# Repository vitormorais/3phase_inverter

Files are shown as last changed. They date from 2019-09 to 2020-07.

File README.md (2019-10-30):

# 3-phase Power Inverter Development Repository

### Important Information for SELE

- The guide to use the setup is presented in [Guide](https://github.com/vitormorais/3phase_inverter/raw/master/1.%20Functional/guide.docx)
- The repository to import with DAVE is present in [DAVE Project](https://github.com/vitormorais/3phase_inverter/raw/master/4.%20Software_WS/SELE_initialProject.zip)

### Features

- The 3-phase 30A@450V power inverter for academic/research purposes;
- This inverter has built-in measurements of AC currents, AC voltages and DC bus voltage;
- The inverter is based on infineon IPM IKCM30F60GA module (a low-cost module, with integrated drivers);
- The control board is based on XMC4500 Relax (lite) kit, a well known board in UP Laboratory of Power Electronics;
- Reduced cost of hardware (around 100€);

### Motivation

- Decrease the Hardware design, by using a generic multi-purpose power inverter;
- Decrease the Testing time and increase the Validation outcomes;
- Increase in Implementation and Control capabilities, without spending too much time in this step;
- Increase in new contributions to the Scientific Comunity, with more papers.

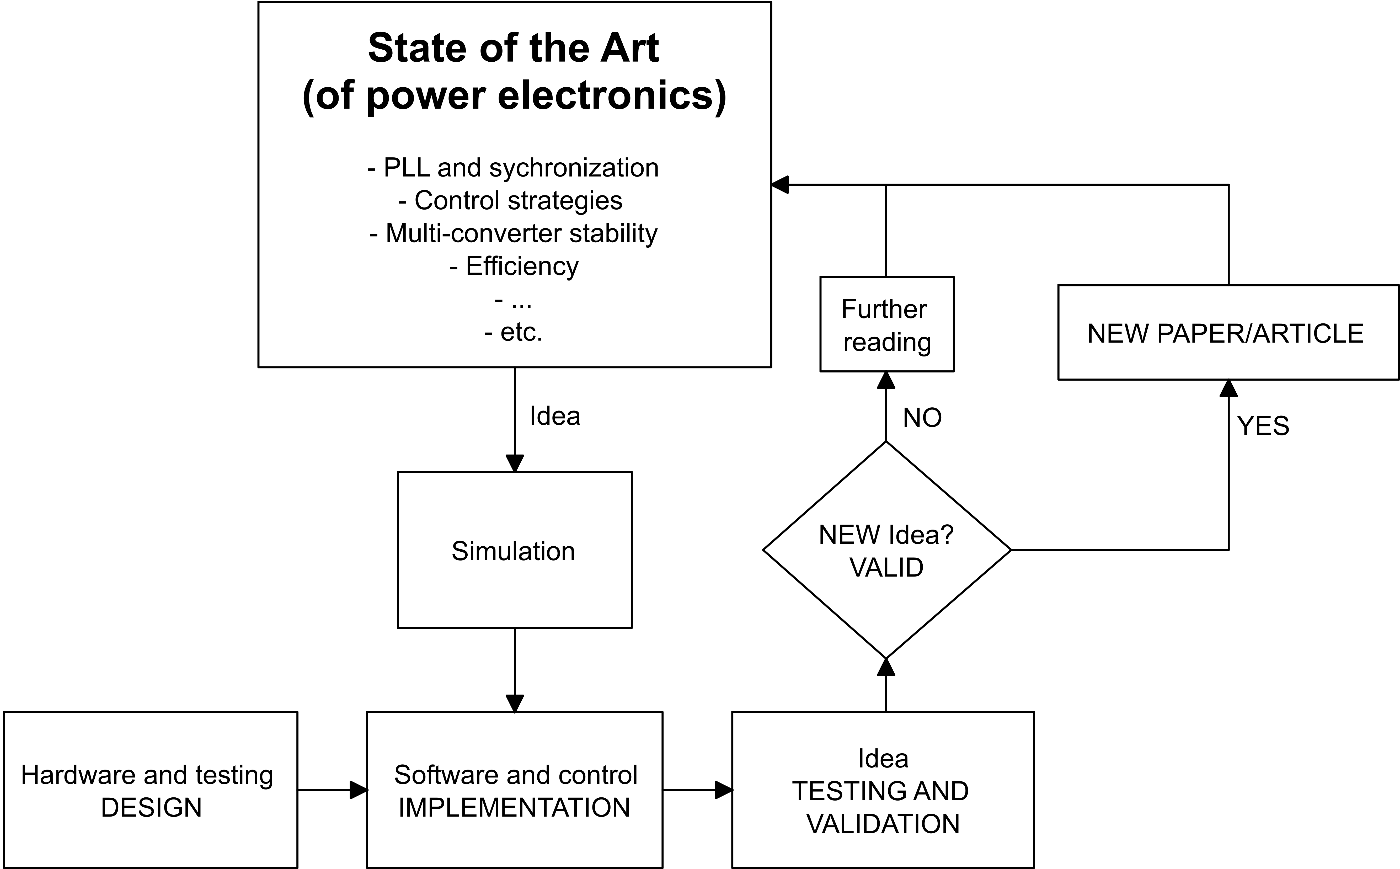
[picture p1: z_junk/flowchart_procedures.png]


------------

### How to use

- TODO

### TODO

- Define functional requirements of this project
- Create BOM for 10 boards (expecting 1000€)
-
- Create "how to use" manual 

------------

### DEMO

#### V2
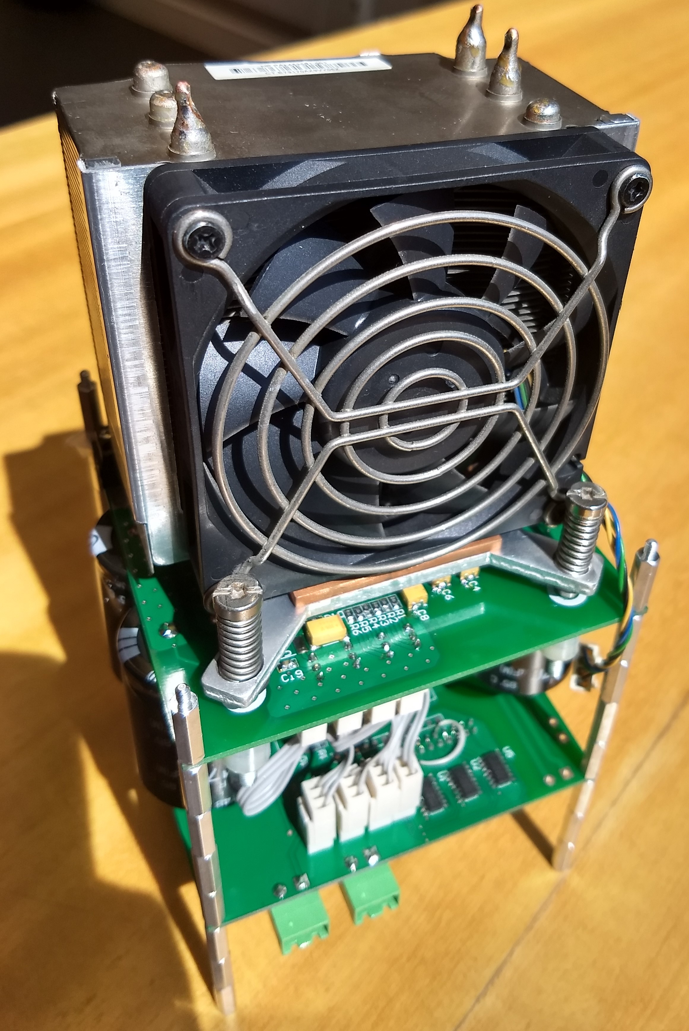
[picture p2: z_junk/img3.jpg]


#### V1
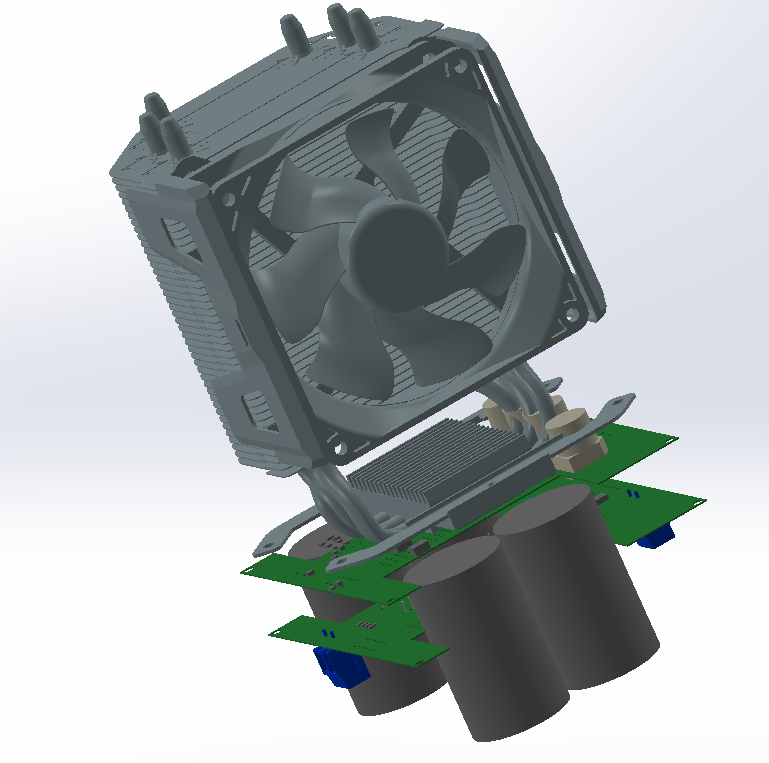
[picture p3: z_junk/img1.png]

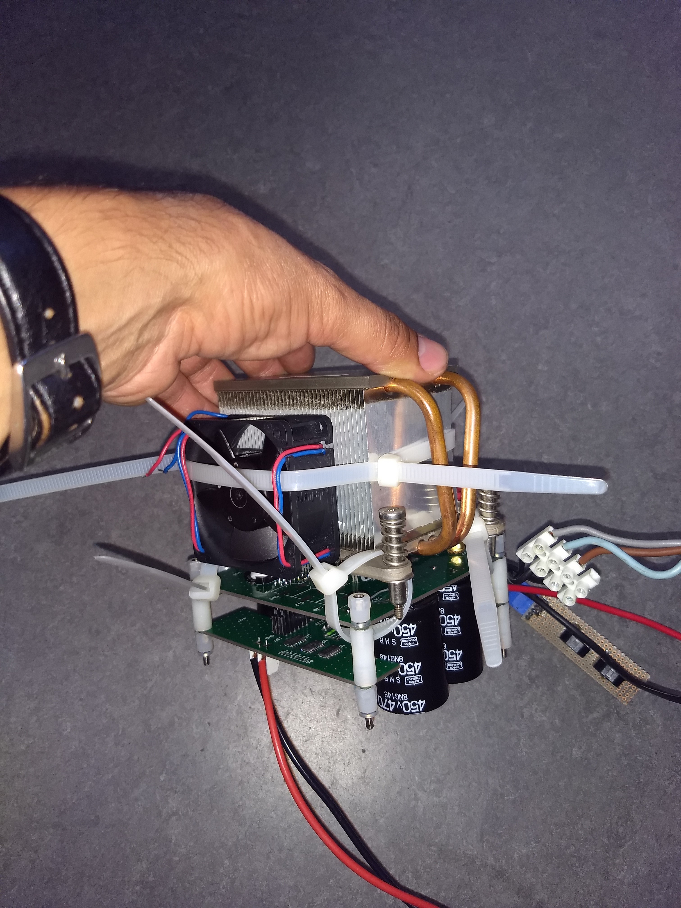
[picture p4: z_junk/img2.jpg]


------------

### Folder structure

| FOLDER | DESCRIPTION  | comments  |
| :--- | :--- | :--- |
|  1. Functional  |  Documentation folder for functional requirements of this project | |
|  2. Hardware PCB  |  Development folder for the PCB hardware  | |
|  3. Design  |  Documentation for the hardware design requirements and BOM | |
|  4. Software_WS  |  Development folder having the DAVE workspace for XMC4500 programming  | |
|  5. Implementation | Documentation and simulation of the simulated models/algorithms |  |
|  6. Testing&Validation | Documentation of the product testing | |
|  z_junk |  folder for not-structured content | | 

### Folder structure (tree)

```bash
├── 1. Functional
│   └── draft.docx
├── 2. Hardware PCB
│   ├── CAMtastic_controlo_rev21.Cam
│   ├── CAMtastic_controlo_rev22.Cam
│   ├── CAMtastic_inversor_rev21.Cam
│   ├── CAMtastic_inversor_rev22.Cam
│   ├── History
│   ├── PCB_controlo_rev2.zip
│   ├── PCB_inversor_rev2.zip
│   ├── __Previews
│   ├── accets
│   ├── controlo_rev2.PcbDoc
│   ├── controlo_rev2.PrjPcb
│   ├── controlo_rev2.PrjPcbStructure
│   ├── controlo_rev2.SchDoc
│   ├── debug.log
│   ├── inversor_rev2.PcbDoc
│   ├── inversor_rev2.PrjPcb
│   ├── inversor_rev2.PrjPcbStructure
│   ├── inversor_rev2.SchDoc
│   ├── vmorais_libraries.PcbLib
│   └── vmorais_libraries.SchLib
├── 3. Design
│   └── BOM.xlsx
├── 4. Software_WS
│   └── OL_VSC_vitor
├── 5. Implementation
│   └── hardware.psimsch
├── 6. Testing&Validation
│   └── testing.docx
├── README.md
├── folder_structure_binary.txt
└── z_junk
    ├── flowchart_procedures.png
    ├── flowchart_procedures.svg
    ├── img1.png
    ├── img2.jpg
    └── img3.jpg
```

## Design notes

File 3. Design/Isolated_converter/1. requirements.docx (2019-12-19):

List of requirements

1. All measurments should be isolated
  a. Current measurement isolation: achieved;
  b. Voltage measurement isolation: achieved;
  c. DC bus voltage measurement: achieved;
  d. Termistor temperature measurement: not achieved
    i. An isolation amplifier should be considered
  e. Fault: to be considered
2. All of the driving signals/pwm should be isolated
  a. Include an isolation DC/DC converter
3. The IPM module must be supplied by an isolation DC/DC converter
  a. Include an isolation DC/DC converter (15.5V)
4. Avoid/reduce the amount of cables
  a. Promote the usage of jumpers

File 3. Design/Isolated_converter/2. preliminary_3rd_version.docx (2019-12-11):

This document presents the possible solution for the final prototype of the converter.

A possible solution will be a middle board between the already developed board and the new board:

1. Consider there the isolation part
2. DC/DC 6W 5V (in: 18 V to 36 V): https://pt.mouser.com/ProductDetail/MEAN-WELL/SCWN06B-05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
3. DC/DC 6W 15V (in: 18 V to 36 V): https://pt.mouser.com/ProductDetail/MEAN-WELL/SCWN06B-15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
4. Considerar o seguinte amplificador de isolamento para medir a temperatura do termistor e a tensão do barramento DC:
  a. http://www.ti.com/product/AMC1211-Q1
5. Atuar relés com dual gate drivers (0,76€):
  a. Relés: Mouser No:653-G6DN-1A-SL-DC5
  b. https://eu.mouser.com/ProductDetail/Microchip-Technology-Micrel/MIC4126YME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
6. Usar isolador digital
7. Usar individual gate drivers (0,864€):
  a. https://eu.mouser.com/ProductDetail/Microchip-Technology-Micrel/MIC44F18YMME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
  b. A tensão de alimentação tem de ser, no máximo, 10V
  c. Corrigido para o seguinte integrado:
  d. https://eu.mouser.com/ProductDetail/IXYS/IX4340NETR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
  e. Circuito lógico para um dos braços: https://circuitverse.org/users/14109/projects/41676
  f. Necessárias 15 nand gates
8. Necessário uma fonte de 5V para o XMC4500 (24->5V não isolada)
9. Necessária uma fonte não isolada 15v-5v para alimentar o circuito de 5V do IPM
10. Necessário manter o circuito de drive, sem enables, com uma resistência no braço superior de 0ohm que permita ligar o sinal de gate do transistor de cima à massa

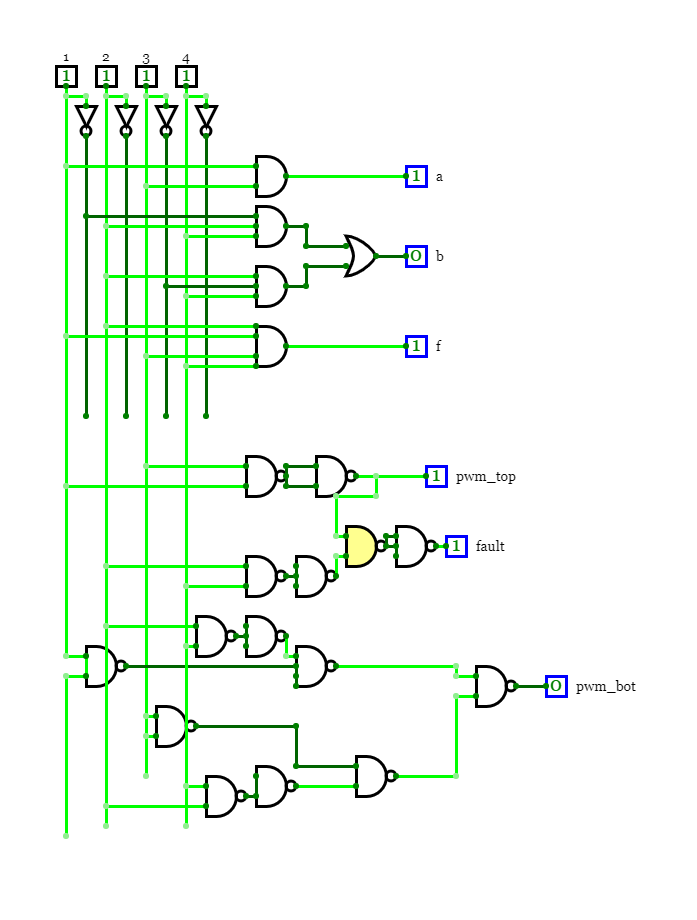
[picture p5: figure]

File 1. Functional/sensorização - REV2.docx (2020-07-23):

# Sensorização - REV2.0

Este documento identifica as lições aprendidas com os sensores empregados no conversor trifásico.

## Sensores de corrente

Foram utilizados sensores directamente ligados aos ADCs. Relativamente aos sensores internos de corrente, foi usado um divisor resistivo para atenuação

Esta estratégia funciona, mas pode facilmente ser melhorada. Por exemplo, a escolha de uma tensão de 3.3V não foi a melhor já que os sensores não estão a funcionar dentro das gamas recomendadas.

1. A escolha do sensor tipo SOIC8 é interessante e poderá ser mantida para correntes até +/- 30A.
2. Poderá ser equacionado ter uma PCB com duas footprints: uma para os sensores SOIC8 e outra para os sensores tipo Alegro 200A. Para correntes superiores, dessolda-se o SOIC8 e solda-se o outro. Do ponto de vista de sensorização, em tese, ambos têm a mesma saída.
3. Layers de electrónica:
  a. A primeira layer após o sensor deverá ser um buffer;
  b. De seguida deverá existir um RC com frequência de corte na ordem de 100kHz;
  c. Then, um circuito amplificador com ganho controlado digitalmente, a ser estudado
  d. Finalmente, toda a electrónica precisa de uma alimentação fixa. Provavelmente a mais indicada deverá ser 5V. Se os sensores precisarem de 3.3V, então, deverão existir reguladores.
4. Para cabo, pode ser equacionada a opção RJ45 blindado CAT7
  a. 1.48€: 1M https://www.castroelectronica.pt/product/cabo-de-rede-rj45-cat7-sftp-1m-cinzento--aisens
  b. Cada conector: 0,66€; do lado do controlo podem ser usados conectores múltiplos

## LOGBOOK sensores de corrente

V0.2 revisão do circuito analógico

Deverá ser alterado o circuito para um amplificador não inversor (senão não funciona)

V0.1

Fig1: esquemático raw, todas as ideias em cima da mesa

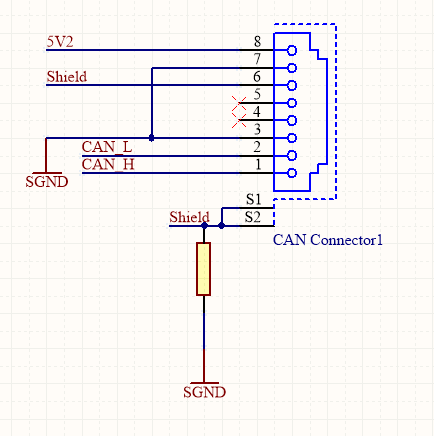
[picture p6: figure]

Fig2: detalhe da implementação atual do CAN

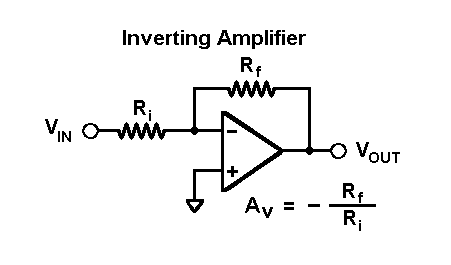
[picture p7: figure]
What is inverting amplifier? - Quora
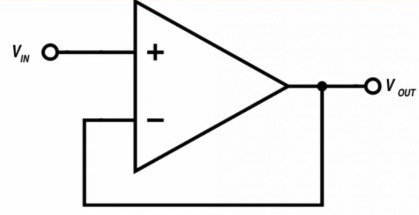
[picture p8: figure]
Applications of the Op-Amp Voltage Follower Circuit - Video Tutorial
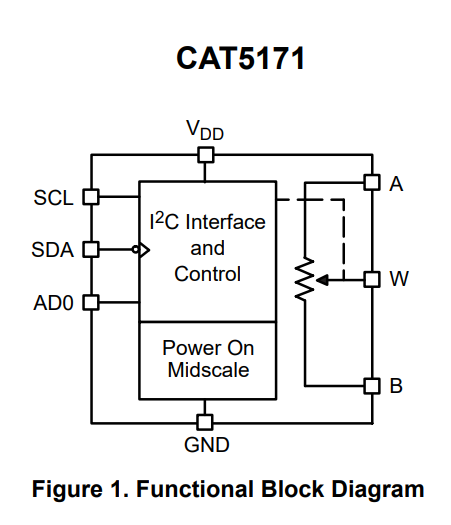
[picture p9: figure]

Fig3: esquemas importantes p/ electrónicas

Tabela 1: Estudo dos custos

funcionalidade | IC | link | custo
Sensor 1 | ACS712ELCTR-20A-T | C10681 (https://lcsc.com/product-detail/Sensors_Allegro-MicroSystems-LLC_ACS712ELCTR-20A-T_Allegro-MicroSystems-LLC-ACS712ELCTR-20A-T_C10681.html/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) | 1,22€ x3
Sensor 1 | ACS770ECB-200B-PFF-T | | 7€ x3
3x buffer + | OPA2350 | C55904 (https://lcsc.com/product-detail/Precision-OpAmps_TI_OPA2350UA-2K5_OPA2350UA-2K5_C55904.html/?href=jlc-SMT) | 3x 1.27€
3x amplifier | OPA2350 | C55904 (https://lcsc.com/product-detail/Precision-OpAmps_TI_OPA2350UA-2K5_OPA2350UA-2K5_C55904.html/?href=jlc-SMT) | 3x 1.27€
3x variable gain | 50 kohm i2c DIGITAL POTENTIOMETER | C154777 (https://lcsc.com/product-detail/Digital-Potentiometer-ICs_ON-Semicon_CAT5171TBI-50GT3_ON-Semicon-ON-CAT5171TBI-50GT3_C154777.html/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) | 3x 0.3679€
5V LDO (?)
3.3V LDO (?)
Microcontroller | STM32F103C8T6 | C8734 (https://lcsc.com/product-detail/ST-Microelectronics_STMicroelectronics_STM32F103C8T6_STM32F103C8T6_C8734.html/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) | 1.3€
OSC uC 16 MHz | X322516MLB4SI | C13738 (https://lcsc.com/product-detail/SMD-Crystal-Resonators_Yangxing-Tech-X322516MLB4SI_C13738.html/?href=jlc-SMT) | 0.08€
CAN (provavelmente n/ isolado) | TJA1050T/CM,118 | C6952 (https://lcsc.com/product-detail/CAN_NXP_TJA1050T-CM-118_TJA1050T-CM-118_C6952.html/?href=jlc-SMT) | 0,396€
Conector RJ45 c/ leds | RJE49-188-1411 | mouser | 4,18€
RC: 100ohm 100pF | Dá 150kHz

Total PCB + ASM aprox 12€

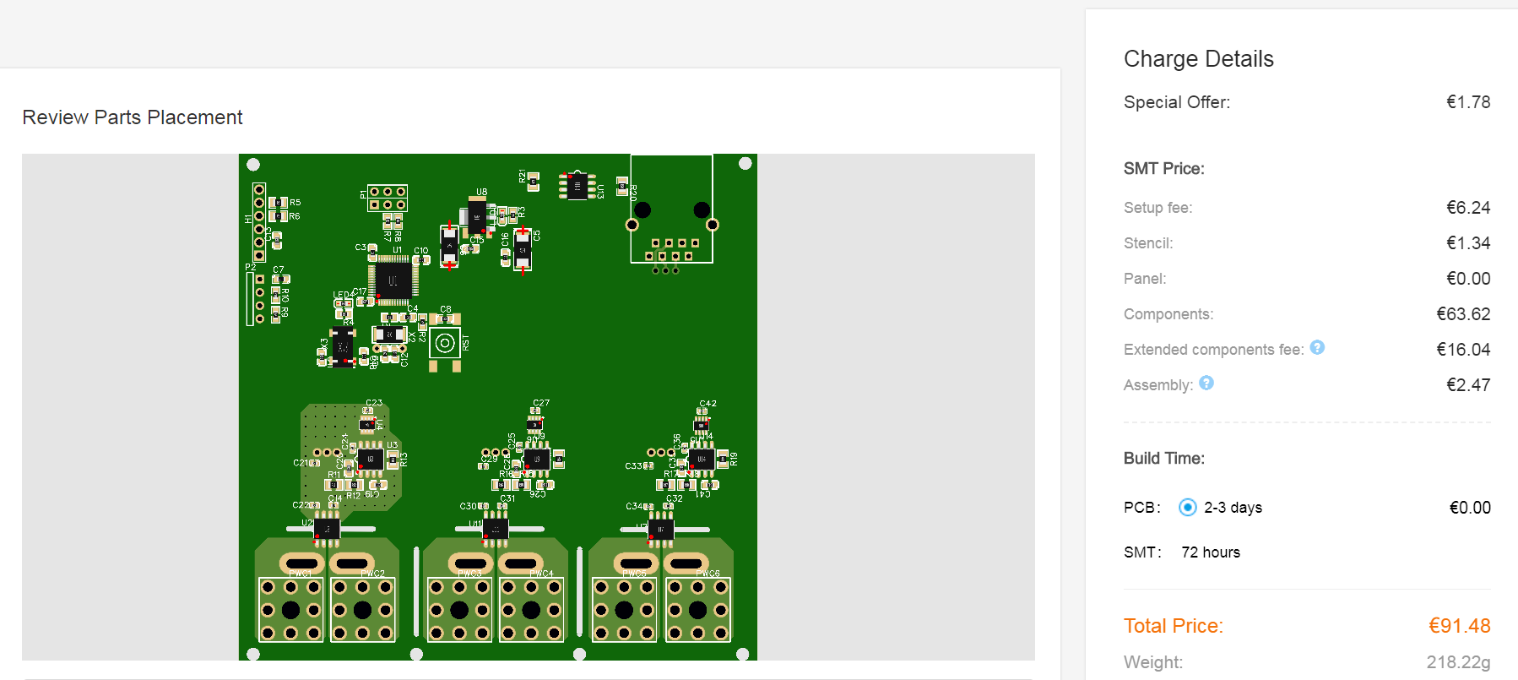
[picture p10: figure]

Preço p/ 10 placas= 160€ aprox (inc. shipping + alfandega)

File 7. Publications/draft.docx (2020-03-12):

# Title

Three-phase Power Inverter for academic purposes: lessons learned from teaching electronics.

# Abstract

Teaching power electronics adequately is a complex task.

Within the strategies found in the literature, the one used in this work includes the use of a simulator. (ver possível plágio do paper do Valter)

This simulator represents the hardware platform for a three-legs inverter, with integrated current and voltage measurements.

Currently, the simulator supports an infineon XMC4500 control board, where the same .c code is used either in the simulator and in the control board.

The hardware setup was first used at a Power Electronics course of the Integrated Master Degree in Electrical and Computing Engineering at the Faculty of Engineering of the University of Porto.

The results of this hardware setup usage in this course shows the students learning process, where several fields of power electronics were acquired, such as control loops, input measurements processing, etc.

In this work, the materials and methods to adequately teach either the simulator and the hardware setup will be presented and discussed.

# Introduction

# Literature review

# Materials

Hardware:

- The 3-phase 30A@450V power inverter for academic/research purposes;
- This inverter has built-in measurements of AC currents, AC voltages and DC bus voltage;
- The inverter is based on infineon IPM IKCM30F60GA module (a low-cost module, with integrated drivers);
- The control board is based on XMC4500 Relax (lite) kit, a well known board in UP Laboratory of Power Electronics;

Software:

- PSIM
- .c block
- Libraries

# Methods

## Step 1: practical demonstration of an example implementation

In this step, an example application of one simple capability is presented and is supported with a guide. It is expected that this step will take 2x 2h

This example considers the hardware setup connected to a 30V DC bus, and the three-phase outputs connected to a RL load. The objective of this demonstration example is to generate an AC output voltage in the inverter, that will be seen as an AC current in the RL load.

The simulation example will have all hardware modelling and a .c block with the code ready to generate the output desired waveforms.

## Step 2: theorical presentation of the libraries

In this step, a few libraries will be presented for general purpose implementations. In this set of libraries, PI controllers, first order low pass filters, Park/Clark transformations, delays, etc are presented.

## Step 3: presentation of the possible applications

In this step, each of the possible applications of power electronics converters that can be implemented with this three-leg converter are presented.

Examples:

- three phase induction motor control;
- three phase inverter
- single phase motor control
- single phase inverter
- DC motor control
- 3x regulated step-down voltage sources
- Interleaved DC/DC step down converter
- Step-up converter for PV applications
- Bi-directional battery charger

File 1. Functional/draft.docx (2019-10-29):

# Sumário

Este documento apresenta as linhas gerais de um projeto focado no desenvolvimento de uma plataforma de desenvolvimento destinada à investigação e/ou ensino de métodos de controlo para conversores eletrónicos de potência, especificamente, inversores.

# Objetivo

Este inversor deverá ser capaz de:

1. Funcionar como amplificador de potência programável com três saídas de sinal (inversor trifásico) e uma entrada de um barramento DC
  a. Deverá proporcionar ensaios sobre cargas trifásicas
2. Funcionar como fonte de corrente controlada
  a. Deverá ser capaz de controlar a corrente de uma carga, independentemente da tensão de alimentação
3. Ter flexibilidade para ligação à rede trifásica
  a. deverá ter contactores ()
  b. deverá ter medida de tensão

Este inversor deverá ser

1. Modular, com drives e comando integrados (tecnologia IPM)
2. Sensorização integrada:
  a. de 3 correntes AC, da tensão DC (obrigatório)
  b. de 3 tensões AC (apenas nos módulos de ligação trifásica)
3. Dotado de algumas protecções
  a. Contactores/relés, apenas se houver necessidade funcional
  b. Desde que não encareça o custo da solução
4. Microcontrolador integrado na solução

Com este inversor, deverá ser submetido um paper para uma conferência na área de PE, possivelmente focado na componente de educação

# Tarefas

1. Desenvolvimento de uma lista de requisitos da solução final
2. Desenvolvimento de esquemas

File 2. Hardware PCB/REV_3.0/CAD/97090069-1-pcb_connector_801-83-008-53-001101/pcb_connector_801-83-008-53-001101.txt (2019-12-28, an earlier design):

"Symbol";"Value";"Unit";
"TraceParts.PartNumber";"10-20122013-099820";"";
"REFERENCE";"801-83-008-53-001101";"";
"TraceParts.PartTitle";"Wire-wrap socket connector 2.54 mm, height 7 mm, 3-level, single row";"";
"TraceParts.InstanceId";"10-20122013-0998203EZ7EX63LKH9MCDKNJ7ZAHDI6";"";
"DESIGN";"Wire-wrap socket connector 2.54 mm, height 7 mm, 3-level, single row, 8 contacts, Tin / 0,75 µm Gold";"";
"TraceParts.PartStatus";"Published";"";
"TraceParts.PartStatusId";"";"";
"SUPPLIER";"preci-dip";"";
"TraceParts.PartVersion";"1.0.6";"";
"TRACEPARTS";"TRACEPARTS";"";
"TraceParts.PartLanguage";"en";"";
"TraceParts.ClassPath";"PRECIDIP:/F_PRECIDIP/PRECIDIP.020/PRECIDIP.020.060/10-20122013-099820";"";

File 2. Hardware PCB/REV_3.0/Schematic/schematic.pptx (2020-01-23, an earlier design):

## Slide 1

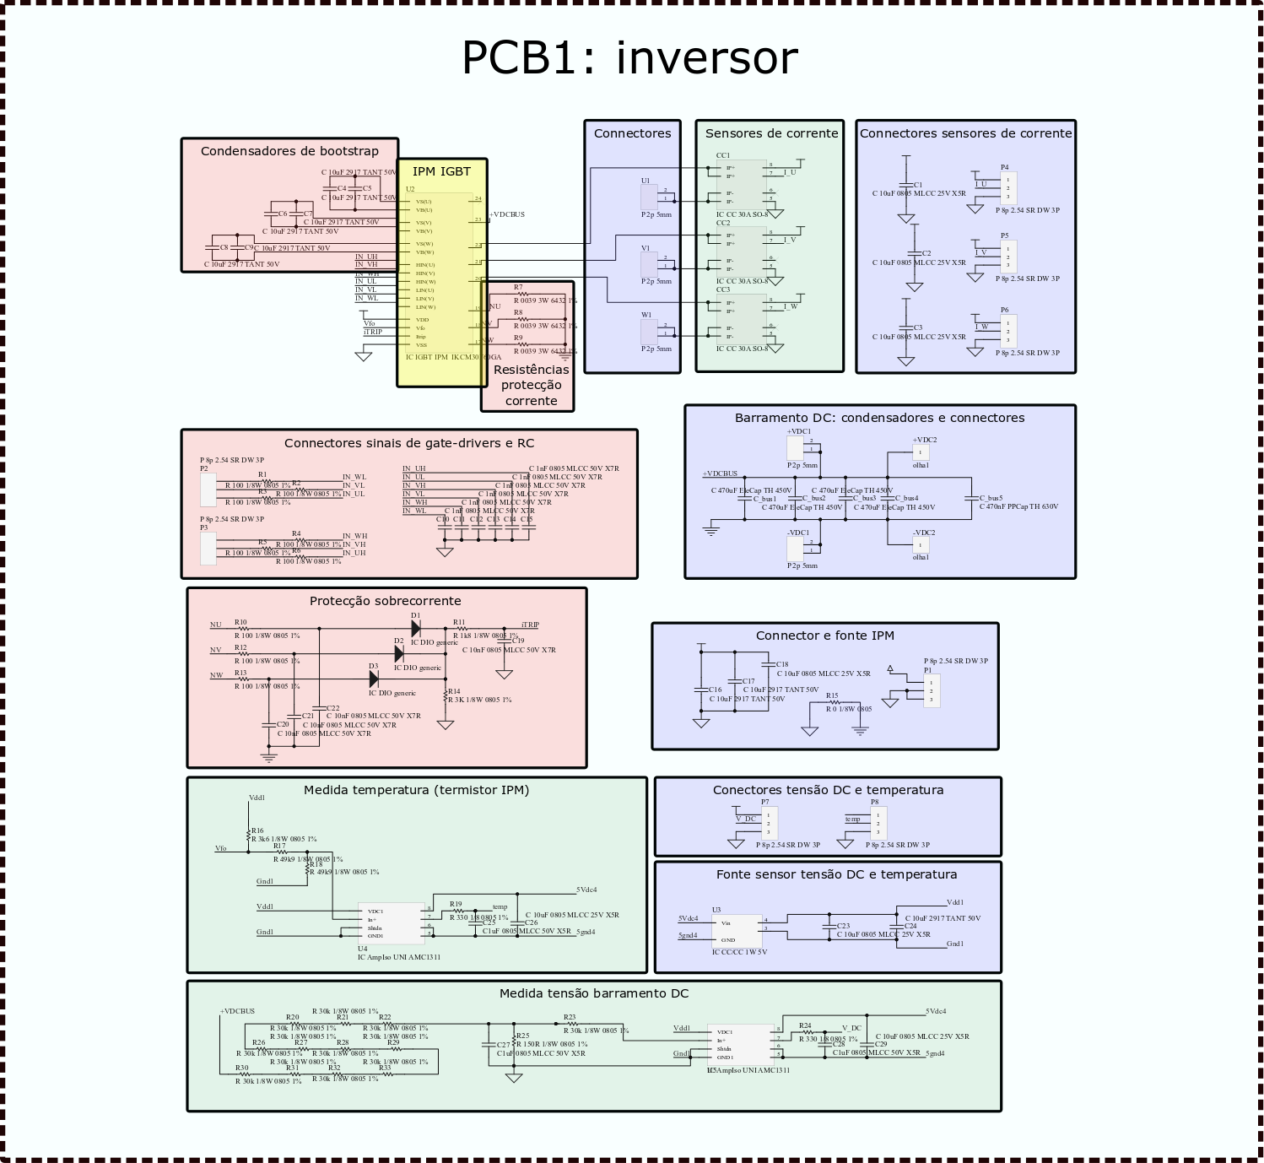
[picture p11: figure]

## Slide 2

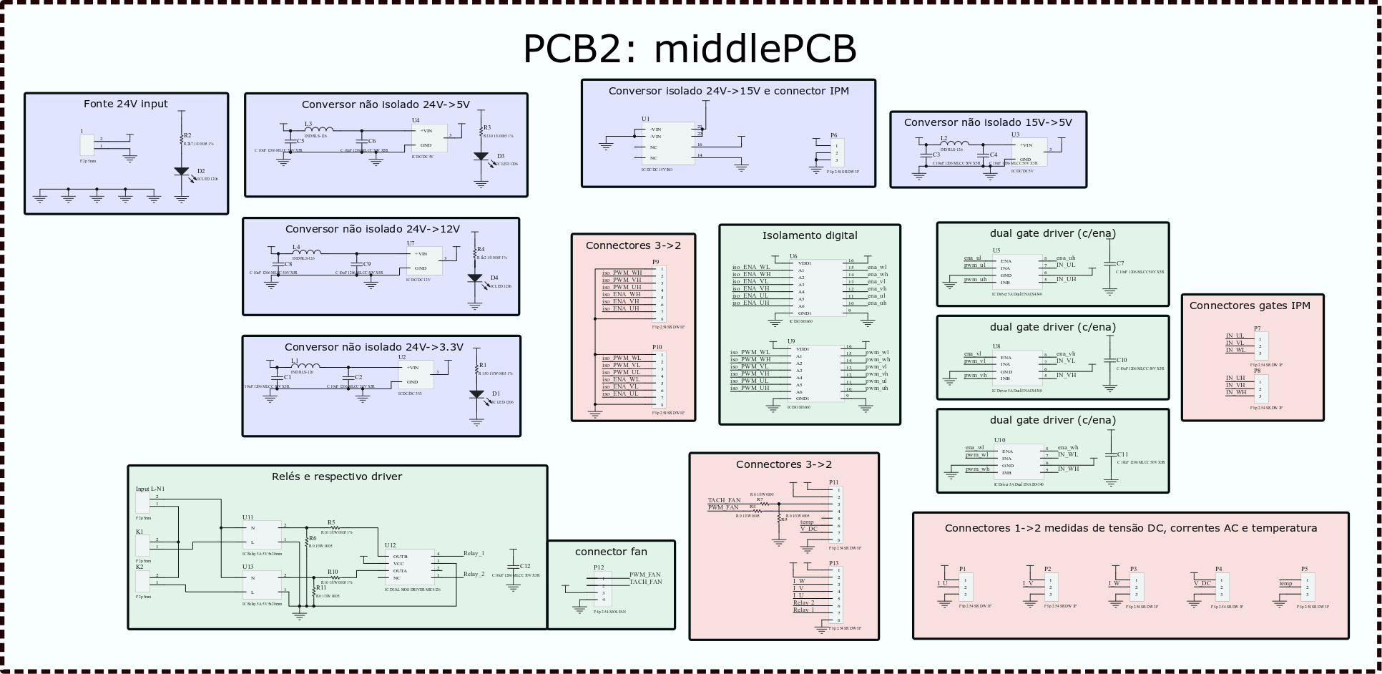
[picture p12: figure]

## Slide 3

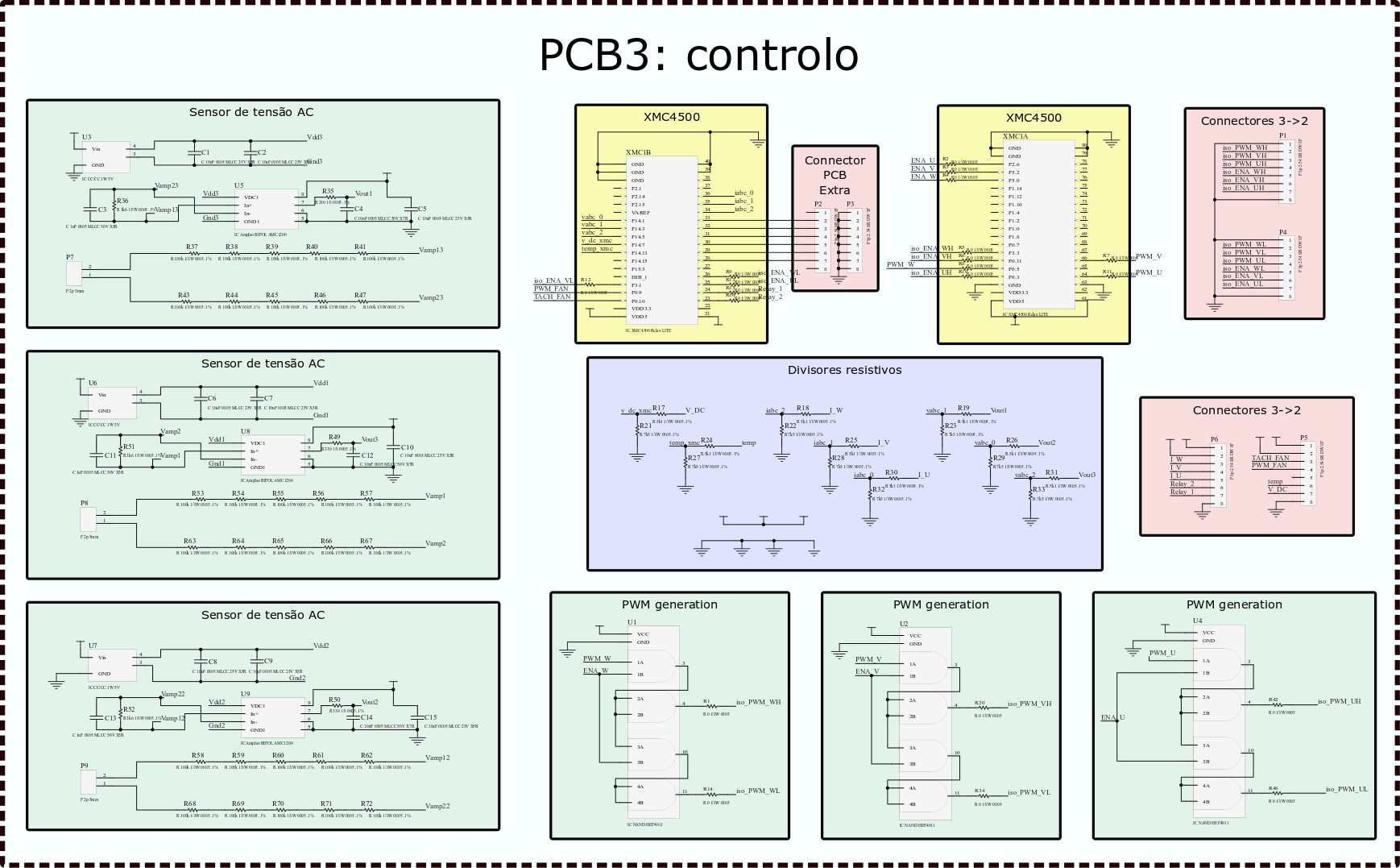
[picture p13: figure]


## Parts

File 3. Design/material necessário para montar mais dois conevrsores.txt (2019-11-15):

temos capacidade de montar mais dois conversores:
---  1 sem medida de tensões AC
---  1 com medida de tensões AC (igual aos demais)

faltam os seguintes componentes:
-- crimps (só dá para fazer 1 conversor)
-- alojamento para crimps (não chega a 1)
-- header para crimps (dá para 1)
-- conector pcb parafuso (pode ser utilizado phoenix)
-- xmc4500 (a pedir na i103)
-- barra de pinos fêmea pcb (a pedir no RC)
-- espaçadores de plástico: a pensar numa estrutura em 3D

resumindo, há capacidade de construção de dois conversores, mas são preciso alguns truques

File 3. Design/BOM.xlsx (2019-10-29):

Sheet: Sheet4
fornecedor | VPN | Description | Quantity | price | price total
RS | 896-6696 | Bloque de terminal PCB, paso5mm 2 Contacto Macho Recta Bloque de terminales PCB, montaje: Montaje en PCB | 20 | 0.240 € | 4.80 €
MOUSER | 963-UMK316BBJ106ML-T | Capacitores de cerâmica multicamada MLCC - SMD/SMT 1206 50V 10uF 20% X5R | 20 | 0.310 € | 6.20 €
MOUSER | 80-T491D106K050AT | Condensadores de tântalo - revestimento sólido de SMD 50V 10uF 10% ESR=0.8Ohms | 20 | 1.580 € | 31.60 €
MOUSER | 603-CC805KRX7R9BB103 | Capacitores de cerâmica multicamada MLCC - SMD/SMT 10nF 50V X7R 10% | 50 | 0.051 € | 2.55 €
MOUSER | 963-TMK212BBJ106KG-T | Capacitores de cerâmica multicamada MLCC - SMD/SMT 10uF 25V X5R +/-10% 0805 Gen Purp | 60 | 0.108 € | 6.48 €
MOUSER | 963-UMK212BJ105MG-T | Capacitores de cerâmica multicamada MLCC - SMD/SMT 0805 50V 1uF 20% X5R | 50 | 0.061 € | 3.05 €
MOUSER | 630-ACHS-7123-000E | Sensores de Corrente de Montagem de Painel Hall Effect IC LF 30A 66 mV/A | 10 | 2.770 € | 27.70 €
MOUSER | 661-ESMR451N471MR40S | Capacitores eletrolíticos de alumínio - terminal de pressão 450V 470uF 20% Tol. | 20 | 5.580 € | 111.60 €
FARNELL | 9751343 | B32653A6474K000 - DC Film Capacitor, 0.47 µF, 630 V, Metallized PP, ± 10%, B32653 Series | 2 | 2.180 € | 4.36 €
MOUSER | 512-1N4148TR | Diodos - Fins gerais, energia, comutação Hi Conductance Fast | 20 | 0.050 € | 1.00 €
MOUSER | 538-105431-1103 | Distribuidores e Alojamento de Fios NANO-FIT HDR SMT VT SGL 3CKT TIN BLK | 20 | 1.490 € | 29.80 €
MOUSER | 538-145130-0300 | Cabos de força DC Nano-Fit 75mm Cbl SR 3Ckt Blk | 10 | 2.920 € | 29.20 €
FARNELL | 1675765 | MC34631 - Wire-To-Board Connector, Vertical, 2.54 mm, 3 Contacts, Header, MC34 Series, Through Hole, 1 Rows | 50 | 0.029 € | 1.46 €
FARNELL | 1675755 | MC34483 - Connector Housing, MC34 Series, Receptacle, 3 Ways, 2.54 mm, 2218T Crimp Contacts | 50 | 0.028 € | 1.38 €
RS | 467-598 | Contacto de terminal de crimpado Molex 08-50-0032, KK, 4809, Hembra, Crimpado, Revestimiento de Estaño | 200 | 0.078 € | 15.60 €
MOUSER | 71-CRCW0805100RFKEAC | Resistores de Filme Espesso - SMD 1/8Watt 100ohms 1% Commercial Use | 50 | 0.047 € | 2.35 €
FARNELL | 2828259 | MCLRP12FTWRR039 - SMD Current Sense Resistor, 0.039 ohm, LRP Series, 2512 [6432 Metric], 3 W, ± 1%, Metal Strip | 20 | 0.257 € | 5.14 €
MOUSER | 652-CR0805JW-362ELF | Resistores de Filme Espesso - SMD 3.6K 5% | 10 | 0.034 € | 0.34 €
MOUSER | 71-CRCW08051K00FKEAC | Resistores de Filme Espesso - SMD 1/8Watt 1Kohms 1% Commercial Use | 10 | 0.055 € | 0.55 €
MOUSER | 755-ESR10EZPJ182 | Resistores de Filme Espesso - SMD 0805 1K8ohm 5% Anti Surge AEC-Q200 | 10 | 0.064 € | 0.64 €
MOUSER | 667-ERJ-6GEYJ302V | Resistores de Filme Espesso - SMD 0805 3Kohms 5% Tol AEC-Q200 | 10 | 0.055 € | 0.55 €
MOUSER | 71-CRCW08050000Z0EAC | Resistores de Filme Espesso - SMD 1/8Watt 0ohms Commercial Use | 10 | 0.026 € | 0.26 €
MOUSER | 667-ERJ-6ENF3002V | Resistores de Filme Espesso - SMD 0805 30Kohms 1% AEC-Q200 | 200 | 0.020 € | 4.00 €
MOUSER | 71-CRCW0805330RFKEAC | Resistores de Filme Espesso - SMD 1/8Watt 330ohms 1% Commercial Use | 30 | 0.047 € | 1.41 €
MOUSER | 71-CRCW0805-150-E3 | Resistores de Filme Espesso - SMD 1/8watt 150ohms 1% 100ppm | 30 | 0.059 € | 1.77 €
MOUSER | 726-IKCM30F60GDXKMA1 | Controladores e drivers de Motor/Movimento/Ignição IFPS MODULES | 4 | 16.250 € | 65.00 €
MOUSER | 919-RFB-0505S | Conversores CC/CC com isolação 1W 5Vin 5Vout 200mA SIP7 | 15 | 1.370 € | 20.55 €
MOUSER | 595-AMC1200BDWVR | Amplificadores de isolamento 4kV peak Iso Amp | 12 | 4.150 € | 49.80 €
MOUSER | 604-APT3216SGC | LEDs padrão - SMD GREEN WATER CLEAR | 10 | 0.281 € | 2.81 €
MOUSER | 71-CRCW08055K60FKEA | Resistores de Filme Espesso - SMD 1/8watt 5.6Kohms 1% | 50 | 0.059 € | 2.95 €
MOUSER | 667-ERJ-6ENF7501V | Resistores de Filme Espesso - SMD 0805 7.5Kohms 1% AEC-Q200 | 50 | 0.073 € | 3.65 €
MOUSER | 771-HEF4011BTD-T | Portas lógicas QUADRUPLE 2-INPUT NAND GATE | 10 | 0.305 € | 3.05 €
MOUSER | 558-MCX240D5 | Relês - Montagem do PCB SIP SSR 280VAC/5A 3-15VDC In, ZC | 2 | 16.080 € | 32.16 €

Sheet: BOM (3inv)
Comment | Description | Designator inversor | Designator controlo | Footprint | LibRef | Quantity inversor | Quantity controlo | Quantity TOTAL | fornecedor | VPN | Description | Quantity | price | price total
gen_purpose_conn_1x2 |  | +VDC1, -VDC1, U1, V1, W1 | P2, P4, P11, P12, P13 | connector1x2_parafuso | gen_purpose_conn_1x2 | 5 | 5 | 10 | RS | 896-6696 | Bloque de terminal PCB, paso5mm 2 Contacto Macho Recta Bloque de terminales PCB, montaje: Montaje en PCB | 20 | 0.240 € | 4.80 €
Capacitor SMD | 10uF | C1, C2, C3, C11, C22 |  | CAPC_1206 | Capacitor SMD | 5 |  | 5 | MOUSER | 963-UMK316BBJ106ML-T | Capacitores de cerâmica multicamada MLCC - SMD/SMT 1206 50V 10uF 20% X5R | 20 | 0.310 € | 6.20 €
Capacitor TANT | 10uF 50V TANT | C4, C5, C6, C7, C8, C9, C10, C20, C21 |  | CAPC_2917 | tantalum_CAP, tantalum_CAP, tantalum_CAP, tantalum_CAP, tantalum_CAP, tantalum_CAP, Capacitor SMD, Capacitor SMD, Capacitor SMD | 9 |  | 9 | MOUSER | 80-T491D106K050AT | Condensadores de tântalo - revestimento sólido de SMD 50V 10uF 10% ESR=0.8Ohms | 20 | 1.580 € | 31.60 €
Capacitor SMD | 10nF | C12, C13, C14, C15, C16, C17, C18, C19, C23, C24, C25, C26 |  | CAPC_0805 | Capacitor SMD | 10 |  | 10 | MOUSER | 603-CC805KRX7R9BB103 | Capacitores de cerâmica multicamada MLCC - SMD/SMT 10nF 50V X7R 10% | 50 | 0.051 € | 2.55 €
Capacitor SMD | 10uF | C27, C28, C31 | C1, C2, C5, C6, C7, C8, C9, C12, C15 | CAPC_0805 | Capacitor SMD | 3 | 9 | 12 | MOUSER | 963-TMK212BBJ106KG-T | Capacitores de cerâmica multicamada MLCC - SMD/SMT 10uF 25V X5R +/-10% 0805 Gen Purp | 60 | 0.108 € | 6.48 €
Capacitor SMD | 1uF | C29, C30 | C3, C4, C10, C11, C13, C14 | CAPC_0805 | Capacitor SMD | 2 | 6 | 8 | MOUSER | 963-UMK212BJ105MG-T | Capacitores de cerâmica multicamada MLCC - SMD/SMT 0805 50V 1uF 20% X5R | 50 | 0.061 € | 3.05 €
ACHS-7123 |  | CC1, CC2, CC3 |  | CC6303_SOP8 | Current_Sensor_cc6303 | 3 |  | 3 | MOUSER | 630-ACHS-7123-000E | Sensores de Corrente de Montagem de Painel Hall Effect IC LF 30A 66 mV/A | 10 | 2.770 € | 27.70 €
DC_BUS Capacitor | DC_BUS CAP | C_bus1, C_bus2, C_bus3, C_bus4 |  | Capacitor_DCBUS | CAPACITOR_dcbus | 4 |  | 4 | MOUSER | 661-ESMR451N471MR40S | Capacitores eletrolíticos de alumínio - terminal de pressão 450V 470uF 20% Tol. | 20 | 5.580 € | 111.60 €
DC_BUS Capacitor PP | DC_BUS CAP PP | C_bus5 |  | Snubber_cap_0.47uF | CAPACITOR_dcbus | 1 |  | 1 | FARNELL | 9751343 | B32653A6474K000 - DC Film Capacitor, 0.47 µF, 630 V, Metallized PP, ± 10%, B32653 Series | 2 | 2.180 € | 4.36 €
Diode | 1N4148 | D1, D2, D3 |  | Diode_th | Diode | 3 |  | 3 | MOUSER | 512-1N4148TR | Diodos - Fins gerais, energia, comutação Hi Conductance Fast | 20 | 0.050 € | 1.00 €
 |  | P1, P2, P3, P4, P5, P6, P7, P8 |  | HDR1X3 | Header 3 | 8 |  | 16 | MOUSER | 538-105431-1103 | Distribuidores e Alojamento de Fios NANO-FIT HDR SMT VT SGL 3CKT TIN BLK | 20 | 1.490 € | 29.80 € | NÃO TESTADOS
Header 3 | Header, 3 pin | P1, P2, P3, P4, P5, P6, P7, P8 |  | HDR1X3 | Header 3 | 8 |  | 8 | MOUSER | 538-145130-0300 | Cabos de força DC Nano-Fit 75mm Cbl SR 3Ckt Blk | 10 | 2.920 € | 29.20 € | NÃO TESTADOS
 |  | P1, P2, P3, P4, P5, P6, P7, P8 |  | HDR1X3 | Header 3 | 8 |  | 16 | FARNELL | 1675765 | MC34631 - Wire-To-Board Connector, Vertical, 2.54 mm, 3 Contacts, Header, MC34 Series, Through Hole, 1 Rows | 50 | 0.029 € | 1.46 €
Header 3 | Header, 3 pin | P1, P2, P3, P4, P5, P6, P7, P8 |  | HDR1X3 | Header 3 | 8 |  | 16 | FARNELL | 1675755 | MC34483 - Connector Housing, MC34 Series, Receptacle, 3 Ways, 2.54 mm, 2218T Crimp Contacts | 50 | 0.028 € | 1.38 €
Header 3 | Header, 3 pin | P1, P2, P3, P4, P5, P6, P7, P8 |  | HDR1X3 | Header 3 | 8 |  | 48 | RS | 467-598 | Contacto de terminal de crimpado Molex 08-50-0032, KK, 4809, Hembra, Crimpado, Revestimiento de Estaño | 200 | 0.078 € | 15.60 €
Resistor | 100R | R1, R2, R3, R4, R5, R6, R12, R14, R15 |  | RESC_0805 | Resistor | 9 |  | 9 | MOUSER | 71-CRCW0805100RFKEAC | Resistores de Filme Espesso - SMD 1/8Watt 100ohms 1% Commercial Use | 50 | 0.047 € | 2.35 €
Resistor | Current sense resistor | R7, R8, R9 |  | RESC6432X09M | Resistor | 3 |  | 3 | FARNELL | 2828259 | MCLRP12FTWRR039 - SMD Current Sense Resistor, 0.039 ohm, LRP Series, 2512 [6432 Metric], 3 W, ± 1%, Metal Strip | 20 | 0.257 € | 5.14 €
Resistor | 3K6 | R10 |  | RESC_0805 | Resistor | 1 |  | 1 | MOUSER | 652-CR0805JW-362ELF | Resistores de Filme Espesso - SMD 3.6K 5% | 10 | 0.034 € | 0.34 €
Resistor | 1K | R11 | R2, R3, R4 | RESC_0805 | Resistor | 1 | 1 | 2 | MOUSER | 71-CRCW08051K00FKEAC | Resistores de Filme Espesso - SMD 1/8Watt 1Kohms 1% Commercial Use | 10 | 0.055 € | 0.55 €
Resistor | 1K8 | R13 |  | RESC_0805 | Resistor | 1 |  | 1 | MOUSER | 755-ESR10EZPJ182 | Resistores de Filme Espesso - SMD 0805 1K8ohm 5% Anti Surge AEC-Q200 | 10 | 0.064 € | 0.64 €
Resistor | 3K | R16 | R1 | RESC_0805 | Resistor | 1 | 1 | 2 | MOUSER | 667-ERJ-6GEYJ302V | Resistores de Filme Espesso - SMD 0805 3Kohms 5% Tol AEC-Q200 | 10 | 0.055 € | 0.55 €
Resistor | 0R | R17 |  | RESC_0805 | Resistor | 1 |  | 1 | MOUSER | 71-CRCW08050000Z0EAC | Resistores de Filme Espesso - SMD 1/8Watt 0ohms Commercial Use | 10 | 0.026 € | 0.26 €
Resistor | 30K | R18, R19, R20, R21, R24, R25, R26, R27 | R19, R20, R21, R22, R23, R26, R27, R28, R29, R30, R37, R38, R39, R40, R41, R42, R43, R44, R45, R46, R47, R48, R49, R50, R51, R52, R53, R54, R55, R56 | RESC_0805 | Resistor | 8 | 30 | 38 | MOUSER | 667-ERJ-6ENF3002V | Resistores de Filme Espesso - SMD 0805 30Kohms 1% AEC-Q200 | 200 | 0.020 € | 4.00 €
Resistor | 330R | R22 | R13, R33, R34 | RESC_0805 | Resistor | 1 | 3 | 4 | MOUSER | 71-CRCW0805330RFKEAC | Resistores de Filme Espesso - SMD 1/8Watt 330ohms 1% Commercial Use | 30 | 0.047 € | 1.41 €
R_MEAS | 150R (250R) | R23 | R15, R35, R36 | RESC_0805 | Resistor | 1 | 3 | 4 | MOUSER | 71-CRCW0805-150-E3 | Resistores de Filme Espesso - SMD 1/8watt 150ohms 1% 100ppm | 30 | 0.059 € | 1.77 €
IKCM30F60GA | Intelligent Power Module 600V@30A | U2 |  | ikcm30f60ga | IKCM30F60GA | 1 |  | 1 | MOUSER | 726-IKCM30F60GDXKMA1 | Controladores e drivers de Motor/Movimento/Ignição IFPS MODULES | 4 | 16.250 € | 65.00 €
DC/DC_ISO | DC/DC_ISO | U3 | U3, U6, U7 | DC/DC_ISO | DC/DC_ISO | 1 | 3 | 4 | MOUSER | 919-RFB-0505S | Conversores CC/CC com isolação 1W 5Vin 5Vout 200mA SIP7 | 15 | 1.370 € | 20.55 €
AMC1200 |  | U4 | U4, U8, U9 | SOIC8 | AMC1200 | 1 | 3 | 4 | MOUSER | 595-AMC1200BDWVR | Amplificadores de isolamento 4kV peak Iso Amp | 12 | 4.150 € | 49.80 €
LED | LED |  | D1, D2 | DIODE_1206 | LED |  | 2 | 2 | MOUSER | 604-APT3216SGC | LEDs padrão - SMD GREEN WATER CLEAR | 10 | 0.281 € | 2.81 €
Resistor | 5K |  | R5, R6, R9, R11, R14, R16, R24, R31 | RESC_0805 | Resistor |  | 8 | 8 | MOUSER | 71-CRCW08055K60FKEA | Resistores de Filme Espesso - SMD 1/8watt 5.6Kohms 1% | 50 | 0.059 € | 2.95 €
Resistor | 7K5 |  | R7, R8, R10, R12, R17, R18, R25, R32 | RESC_0805 | Resistor |  | 8 | 8 | MOUSER | 667-ERJ-6ENF7501V | Resistores de Filme Espesso - SMD 0805 7.5Kohms 1% AEC-Q200 | 50 | 0.073 € | 3.65 €
HEF4011 | HEF4011 |  | U1, U2, U5 | SOIC-14N | HEF4011 |  | 3 | 3 | MOUSER | 771-HEF4011BTD-T | Portas lógicas QUADRUPLE 2-INPUT NAND GATE | 10 | 0.305 € | 3.05 €
SSR_D3805 | SSR_D3805 |  |  |  | MCX240D5 | 0 | 2 | 2 | MOUSER | 558-MCX240D5 | Relês - Montagem do PCB SIP SSR 280VAC/5A 3-15VDC In, ZC | 2 | 16.080 € | 32.16 €
XMC4500 | XMC4500 |  |  |  | XMC4500 |  | 1 | 1 | FARNELL | 2443552 | KIT_XMC45_RELAX_LITE_V1 - Evaluation Board, XMC4500 MCU, Detachable On-Board Debugger, USB Powered | 2 | 11.400 € | 22.80 €
XMC male bars | XMC male bars |  |  |  | XMC male bars |  | 2 | 2 | RS | 251-8418 | Cabezal de pines, RS PRO, Recta 72 pines 2 filas paso 2.54mm, Terminación Soldada, Orificio Pasante | 10 | 3.228 € | 32.28 €
XMC female bars | XMC female bars |  |  |  | XMC female bars |  | 2 | 2 | RS | 674-2369 | Conector hembra para PCB ASSMANN WSW Recta 40 pines 2 filas paso 2.54mm Montaje Orificio Pasante | 5 | 1.686 € | 8.43 €
suporte dissipador | suporte dissipador |  |  |  |  | 4 |  | 4 | RS | 102-6570 | HEX. THREADED SPACER 8IO/10 | 20 | 0.337 € | 6.74 €
phoenix male |  |  |  |  |  | 3 | 2 | 5 | FARNELL | 1641993 | 691313510002 - Terminal Block, Header, 5.08 mm, 2 Ways, 20 A, 300 V, Through Hole Right Angle | 20 | 0.235 € | 4.70 €
phoenix female |  |  |  |  |  | 3 | 2 | 5 | RS | 897-1159 | Bloque de terminal PCB, paso5mm 2 Contacto Hembra Ángulo de 90° Macho, montaje: Montaje en PCB | 20 | 0.416 € | 8.32 €
espaçadores M3 |  |  |  |  |  |  |  | 36 | FARNELL | 1733428 | D01496 - Standoff, Nylon 6.6 (Polyamide 6.6), M3, Hex Male-Female, 10 mm, 16 mm | 110 | 0.106 € | 11.66 €
 |  |  |  |  |  |  |  |  |  |  |  |  | TOTAL | 568.68 €
 |  |  |  |  |  |  |  |  |  |  | FALTA
 |  |  |  |  |  |  |  |  |  |  | relé de estado sólido
 |  |  |  |  |  |  |  |  |  |  | XMC4500
 |  |  |  |  |  |  |  |  |  |  | espaçadores
 |  |  |  |  |  |  |  |  |  |  | terminais molex
 |  |  |  |  |  |  |  |  |  |  | conectores xmc4500
 |  |  |  |  |  |  |  |  |  |  | espaçadores suporte dissipador
 |  |  |  |  |  |  |  |  |  |  | conectores phoenix

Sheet: BOM
Comment | Description | Designator inversor | Designator controlo | Footprint | LibRef | Quantity inversor | Quantity controlo | Quantity TOTAL | MOUSER | Description | Quantity | price | price total
gen_purpose_conn_1x2 |  | +VDC1, -VDC1, U1, V1, W1 | P2, P4, P11, P12, P13 | connector1x2_parafuso | gen_purpose_conn_1x2 | 5 | 5 | 10 | 172-2555 (rs) | Bloque de terminal PCB, paso5mm 2 Contacto Macho Recta Bloque de terminales PCB, montaje: Montaje en PCB | 50 | 0.24 € | 12.00 €
Capacitor SMD | 10uF | C1, C2, C3, C11, C22 |  | CAPC_1206 | Capacitor SMD | 5 |  | 5 | 963-UMK316BBJ106ML-T | Capacitores de cerâmica multicamada MLCC - SMD/SMT 1206 50V 10uF 20% X5R | 30 | 0.31 € | 9.30 €
Capacitor TANT | 10uF 50V TANT | C4, C5, C6, C7, C8, C9, C10, C20, C21 |  | CAPC_2917 | tantalum_CAP, tantalum_CAP, tantalum_CAP, tantalum_CAP, tantalum_CAP, tantalum_CAP, Capacitor SMD, Capacitor SMD, Capacitor SMD | 9 |  | 9 | 80-T491D106K050AT | Condensadores de tântalo - revestimento sólido de SMD 50V 10uF 10% ESR=0.8Ohms | 50 | 1.58 € | 79.00 €
Capacitor SMD | 10nF | C12, C13, C14, C15, C16, C17, C18, C19, C23, C24, C25, C26 |  | CAPC_0805 | Capacitor SMD | 10 |  | 10 | 603-CC805KRX7R9BB103 | Capacitores de cerâmica multicamada MLCC - SMD/SMT 10nF 50V X7R 10% | 50 | 0.05 € | 2.55 €
Capacitor SMD | 10uF | C27, C28, C31 | C1, C2, C5, C6, C7, C8, C9, C12, C15 | CAPC_0805 | Capacitor SMD | 3 | 9 | 12 | 963-TMK212BBJ106KG-T | Capacitores de cerâmica multicamada MLCC - SMD/SMT 10uF 25V X5R +/-10% 0805 Gen Purp | 60 | 0.11 € | 6.48 €
Capacitor SMD | 1uF | C29, C30 | C3, C4, C10, C11, C13, C14 | CAPC_0805 | Capacitor SMD | 2 | 6 | 8 | 963-UMK212BJ105MG-T | Capacitores de cerâmica multicamada MLCC - SMD/SMT 0805 50V 1uF 20% X5R | 50 | 0.06 € | 3.05 €
ACHS-7123 |  | CC1, CC2, CC3 |  | CC6303_SOP8 | Current_Sensor_cc6303 | 3 |  | 3 | 630-ACHS-7123-000E | Sensores de Corrente de Montagem de Painel Hall Effect IC LF 30A 66 mV/A | 20 | 2.77 € | 55.40 €
DC_BUS Capacitor | DC_BUS CAP | C_bus1, C_bus2, C_bus3, C_bus4 |  | Capacitor_DCBUS | CAPACITOR_dcbus | 4 |  | 4 | 661-ESMR451N471MR40S | Capacitores eletrolíticos de alumínio - terminal de pressão 450V 470uF 20% Tol. | 20 | 5.58 € | 111.60 €
DC_BUS Capacitor PP | DC_BUS CAP PP | C_bus5 |  | Snubber_cap_0.47uF | CAPACITOR_dcbus | 1 |  | 1 | 9751343 (farnell) | B32653A6474K000 - DC Film Capacitor, 0.47 µF, 630 V, Metallized PP, ± 10%, B32653 Series | 5 | 2.18 € | 10.90 €
Diode | 1N4148 | D1, D2, D3 |  | Diode_th | Diode | 3 |  | 3 | 512-1N4148TR | Diodos - Fins gerais, energia, comutação Hi Conductance Fast | 20 | 0.05 € | 1.00 €
Header 4 | Header, 3 pin | P1, P2, P3, P4, P5, P6, P7, P8 |  |  |  | 8 | 8 | 16 | HW-03-14-G-S-1218-055-ND (digikey) | 3 Position Header Spacer Connector 0.100" (2.54mm) Gold Through Hole | 1 | 0.80 € | 0.80 € | ver alternativas
Header 3 | Header, 3 pin | P1, P2, P3, P4, P5, P6, P7, P8 |  | HDR1X3 | Header 3 | 8 |  | 8 | TMM-124-03-G-S-ND (digikey) | Connector Header position | 1 | 3.55 € | 3.55 € | ver alternativas
Resistor | 100R | R1, R2, R3, R4, R5, R6, R12, R14, R15 |  | RESC_0805 | Resistor | 9 |  | 9 | 71-CRCW0805100RFKEAC | Resistores de Filme Espesso - SMD 1/8Watt 100ohms 1% Commercial Use | 50 | 0.05 € | 2.35 €
Resistor | Current sense resistor | R7, R8, R9 |  | RESC6432X09M | Resistor | 3 |  | 3 | 2828259 (farnell) | MCLRP12FTWRR039 - SMD Current Sense Resistor, 0.039 ohm, LRP Series, 2512 [6432 Metric], 3 W, ± 1%, Metal Strip | 20 | 0.26 € | 5.14 €
Resistor | 3K6 | R10 |  | RESC_0805 | Resistor | 1 |  | 1 | 652-CR0805JW-362ELF | Resistores de Filme Espesso - SMD 3.6K 5% | 10 | 0.03 € | 0.34 €
Resistor | 1K | R11 | R2, R3, R4 | RESC_0805 | Resistor | 1 | 1 | 2 | 71-CRCW08051K00FKEAC | Resistores de Filme Espesso - SMD 1/8Watt 1Kohms 1% Commercial Use | 10 | 0.06 € | 0.55 €
Resistor | 1K8 | R13 |  | RESC_0805 | Resistor | 1 |  | 1 | 755-ESR10EZPJ182 | Resistores de Filme Espesso - SMD 0805 1K8ohm 5% Anti Surge AEC-Q200 | 10 | 0.06 € | 0.64 €
Resistor | 3K | R16 | R1 | RESC_0805 | Resistor | 1 | 1 | 2 | 667-ERJ-6GEYJ302V | Resistores de Filme Espesso - SMD 0805 3Kohms 5% Tol AEC-Q200 | 10 | 0.06 € | 0.55 €
Resistor | 0R | R17 |  | RESC_0805 | Resistor | 1 |  | 1 | 71-CRCW08050000Z0EAC | Resistores de Filme Espesso - SMD 1/8Watt 0ohms Commercial Use | 10 | 0.03 € | 0.26 €
Resistor | 30K | R18, R19, R20, R21, R24, R25, R26, R27 | R19, R20, R21, R22, R23, R26, R27, R28, R29, R30, R37, R38, R39, R40, R41, R42, R43, R44, R45, R46, R47, R48, R49, R50, R51, R52, R53, R54, R55, R56 | RESC_0805 | Resistor | 8 | 30 | 38 | 667-ERJ-6ENF3002V | Resistores de Filme Espesso - SMD 0805 30Kohms 1% AEC-Q200 | 200 | 0.02 € | 4.00 €
Resistor | 330R | R22 | R13, R33, R34 | RESC_0805 | Resistor | 1 | 3 | 4 | 71-CRCW0805330RFKEAC | Resistores de Filme Espesso - SMD 1/8Watt 330ohms 1% Commercial Use | 30 | 0.05 € | 1.41 €
R_MEAS | 150R (250R) | R23 | R15, R35, R36 | RESC_0805 | Resistor | 1 | 3 | 4 | 71-CRCW0805-150-E3 | Resistores de Filme Espesso - SMD 1/8watt 150ohms 1% 100ppm | 30 | 0.06 € | 1.77 €
IKCM30F60GA | Intelligent Power Module 600V@30A | U2 |  | ikcm30f60ga | IKCM30F60GA | 1 |  | 1 | 726-IKCM30F60GDXKMA1 | Controladores e drivers de Motor/Movimento/Ignição IFPS MODULES | 6 | 16.25 € | 97.50 €
DC/DC_ISO | DC/DC_ISO | U3 | U3, U6, U7 | DC/DC_ISO | DC/DC_ISO | 1 | 3 | 4 | 919-RFB-0505S | Conversores CC/CC com isolação 1W 5Vin 5Vout 200mA SIP7 | 25 | 1.31 € | 32.75 €
AMC1200 |  | U4 | U4, U8, U9 | SOIC8 | AMC1200 | 1 | 3 | 4 | 595-AMC1200BDWVR | Amplificadores de isolamento 4kV peak Iso Amp | 20 | 4.15 € | 83.00 €
LED | LED |  | D1, D2 | DIODE_1206 | LED |  | 2 | 2 | 604-APT3216SGC | LEDs padrão - SMD GREEN WATER CLEAR | 10 | 0.28 € | 2.81 €
Resistor | 5K |  | R5, R6, R9, R11, R14, R16, R24, R31 | RESC_0805 | Resistor |  | 8 | 8 | 71-CRCW08055K60FKEA | Resistores de Filme Espesso - SMD 1/8watt 5.6Kohms 1% | 50 | 0.06 € | 2.95 €
Resistor | 7K5 |  | R7, R8, R10, R12, R17, R18, R25, R32 | RESC_0805 | Resistor |  | 8 | 8 | 667-ERJ-6ENF7501V | Resistores de Filme Espesso - SMD 0805 7.5Kohms 1% AEC-Q200 | 50 | 0.07 € | 3.65 €
HEF4011 | HEF4011 |  | U1, U2, U5 | SOIC-14N | HEF4011 |  | 3 | 3 | 771-HEF4011BTD-T | Portas lógicas QUADRUPLE 2-INPUT NAND GATE | 20 | 0.30 € | 6.10 €
 |  |  |  |  |  |  |  |  |  |  |  | TOTAL | 541.40 €
 |  |  |  |  |  |  |  |  |  | FALTA
 |  |  |  |  |  |  |  |  |  | relé de estado sólido
 |  |  |  |  |  |  |  |  |  | XMC4500
 |  |  |  |  |  |  |  |  |  | espaçadores
 |  |  |  |  |  |  |  |  |  | terminais molex
 |  |  |  |  |  |  |  |  |  | conectores xmc4500
 |  |  |  |  |  |  |  |  |  | espaçadores suporte dissipador
 |  |  |  |  |  |  |  |  |  | conectores phoenix

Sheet: Sheet2
Comment | Description | Designator inversor | Designator controlo | Footprint | LibRef | Quantity inversor | Quantity controlo | Quantity TOTAL | LCSC | MOUSER | EBAY/aliexpress | preço ebay/aliexpress
 |  | *1 |  | COOLER | cooler | 1 |  | 1
gen_purpose_conn_1x2 |  | +VDC1, -VDC1, U1, V1, W1 | P2, P4, P11, P12, P13 | connector1x2_parafuso | gen_purpose_conn_1x2 | 5 | 5 | 10 | C138464 | 172-2555 (rs) | https://pt.aliexpress.com/item/32800814802.html | 10pcs 0,58 | 0.58
olhal |  | +VDC2, -VDC2 |  | Olhal | olhal | 2 |  | 2
Capacitor SMD | 10uF | C1, C2, C3, C11, C22 |  | CAPC_1206 | Capacitor SMD | 5 |  | 5 | C13585 | 963-UMK316BBJ106ML-T | https://pt.aliexpress.com/item/32830755495.html | 100pcs 1,54 | 1.54
Capacitor TANT | 10uF 50V TANT | C4, C5, C6, C7, C8, C9, C10, C20, C21 |  | CAPC_2917 | tantalum_CAP, tantalum_CAP, tantalum_CAP, tantalum_CAP, tantalum_CAP, tantalum_CAP, Capacitor SMD, Capacitor SMD, Capacitor SMD | 9 |  | 9 | C224948 | 80-T491D106K050AT | https://pt.aliexpress.com/item/32371133579.html | 10pcs 1,14 | 1.14
Capacitor SMD | 10nF | C12, C13, C14, C15, C16, C17, C18, C19, C23, C24, C25, C26 |  | CAPC_0805 | Capacitor SMD | 10 |  | 10 | C83170 | 603-CC805KRX7R9BB103 | https://pt.aliexpress.com/item/33046583537.html | 100pcs 0,72 | 0.72
Capacitor SMD | 10uF | C27, C28, C31 | C1, C2, C5, C6, C7, C8, C9, C12, C15 | CAPC_0805 | Capacitor SMD | 3 | 9 | 12 | C337995 | 963-TMK212BBJ106KG-T | https://pt.aliexpress.com/item/33046607035.html | 100pcs 0,80 | 0.8
Capacitor SMD | 1uF | C29, C30 | C3, C4, C10, C11, C13, C14 | CAPC_0805 | Capacitor SMD | 2 | 6 | 8 | C282734 | 963-UMK212BJ105MG-T | https://pt.aliexpress.com/item/33046607035.html | 100pcs 0.72 | 0.72
ACHS-7123 |  | CC1, CC2, CC3 |  | CC6303_SOP8 | Current_Sensor_cc6303 | 3 |  | 3 | C286005 | 630-ACHS-7123-000E | https://pt.aliexpress.com/item/32822774478.html | 1pcs 0,91 | 2.73
DC_BUS Capacitor | DC_BUS CAP | C_bus1, C_bus2, C_bus3, C_bus4 |  | Capacitor_DCBUS | CAPACITOR_dcbus | 4 |  | 4 | C46480 | 661-ESMR451N471MR40S | https://pt.aliexpress.com/item/32862387277.html | 2pcs 7,24 | 14.48
DC_BUS Capacitor PP | DC_BUS CAP PP | C_bus5 |  | Snubber_cap_0.47uF | CAPACITOR_dcbus | 1 |  | 1 |  | 3106497 (farnell)
Diode | 1N4148 | D1, D2, D3 |  | Diode_th | Diode | 3 |  | 3 | C14516 | 512-1N4148 | https://pt.aliexpress.com/item/4000022215376.html | 10pcs 0,17 | 0.17
Header 3 | Header, 3 pin | P1, P2, P3, P4, P5, P6, P7, P8 |  | HDR1X3 | Header 3 | 8 |  | 8 |  |  | https://pt.aliexpress.com/item/32896225776.html | 5pcs 4,01 | 4.01
Resistor | 100R | R1, R2, R3, R4, R5, R6, R12, R14, R15 |  | RESC_0805 | Resistor | 9 |  | 9 | C115423 | 71-CRCW0805100RFKEAC | https://pt.aliexpress.com/item/32910302951.html | 100pcs 0,50 | 0.5
Resistor | Current sense resistor | R7, R8, R9 |  | RESC6432X09M | Resistor | 3 |  | 3 | C60734 | 2828259 (farnell) | https://pt.aliexpress.com/item/32284883972.html | 20pcs 4,73 | 4.73
Resistor | 3K6 | R10 |  | RESC_0805 | Resistor | 1 |  | 1 | C1365 | 652-CR0805JW-362ELF | https://pt.aliexpress.com/item/32910302951.html | 100pcs 0,50 | 0.5
Resistor | 1K | R11 | R2, R3, R4 | RESC_0805 | Resistor | 1 | 1 | 2 | C115302 | 71-CRCW08051K00FKEAC | https://pt.aliexpress.com/item/32910302951.html | 100pcs 0,50 | 0.5
Resistor | 1K8 | R13 |  | RESC_0805 | Resistor | 1 |  | 1 | C294692 | 755-ESR10EZPJ182 | https://pt.aliexpress.com/item/32910302951.html | 100pcs 0,50 | 0.5
Resistor | 3K | R16 | R1 | RESC_0805 | Resistor | 1 | 1 | 2 | C25633 | 667-ERJ-6GEYJ302V | https://pt.aliexpress.com/item/32910302951.html | 100pcs 0,50 | 0.5
Resistor | 0R | R17 |  | RESC_0805 | Resistor | 1 |  | 1 | C101922 | 71-CRCW08050000Z0EAC | https://pt.aliexpress.com/item/32910302951.html | 100pcs 0,50 | 0.5
Resistor | 30K | R18, R19, R20, R21, R24, R25, R26, R27 | R19, R20, R21, R22, R23, R26, R27, R28, R29, R30, R37, R38, R39, R40, R41, R42, R43, R44, R45, R46, R47, R48, R49, R50, R51, R52, R53, R54, R55, R56 | RESC_0805 | Resistor | 8 | 30 | 38 | C40087 | 667-ERJ-6ENF3002V | https://pt.aliexpress.com/item/32910302951.html | 100pcs 0,50 | 0.5
Resistor | 330R | R22 | R13, R33, R34 | RESC_0805 | Resistor | 1 | 3 | 4 | C119075 | 71-CRCW0805330RFKEAC | https://pt.aliexpress.com/item/32910302951.html | 100pcs 0,50 | 0.5
R_MEAS | 150R (250R) | R23 | R15, R35, R36 | RESC_0805 | Resistor | 1 | 3 | 4 | C139920 | 667-ERJ-6GEYJ151V | https://pt.aliexpress.com/item/32910302951.html | 100pcs 0,50 | 0.5
IKCM30F60GA | Intelligent Power Module 600V@30A | U2 |  | ikcm30f60ga | IKCM30F60GA | 1 |  | 1 |  | 726-IKCM30F60GDXKMA1 | https://pt.aliexpress.com/item/32854641564.html | 1pc 10,36 | 10.36
DC/DC_ISO | DC/DC_ISO | U3 | U3, U6, U7 | DC/DC_ISO | DC/DC_ISO | 1 | 3 | 4 | C98815 | 919-RFB-0505S | https://pt.aliexpress.com/item/33044998237.html | 2pcs 2,76 | 5.52
AMC1200 |  | U4 | U4, U8, U9 | SOIC8 | AMC1200 | 1 | 3 | 4 | C79905 | 595-AMC1200BDWVR | https://pt.aliexpress.com/item/33051365735.html | 1pc 1,19 | 4.76
LED | LED |  | D1, D2 | DIODE_1206 | LED |  | 2 | 2 | C375460 | 604-APT3216SGC | https://pt.aliexpress.com/item/32686503752.html | 100pcs 0,33 | 0.33
Resistor | 5K |  | R5, R6, R9, R11, R14, R16, R24, R31 | RESC_0805 | Resistor |  | 8 | 8 | C332873 | 71-CRCW0805-5K | https://pt.aliexpress.com/item/32910302951.html | 100pcs 0,50 | 0.5
Resistor | 7K5 |  | R7, R8, R10, R12, R17, R18, R25, R32 | RESC_0805 | Resistor |  | 8 | 8 | C26027 | 667-ERJ-6ENF7501V | https://pt.aliexpress.com/item/32910302951.html | 100pcs 0,50 | 0.5
HEF4011 | HEF4011 |  | U1, U2, U5 | SOIC-14N | HEF4011 |  | 3 | 3 | C6725 | 771-HEF4011BTD-T | https://pt.aliexpress.com/item/32422820267.html | 10pcs 0,68 | 0.68

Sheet: Sheet1
Comment | Description | Designator | Footprint | LibRef | Quantity | LCSC | MOUSER | EBAY/aliexpress | preço ebay
IKCM30F60GA |  | *2 | ikcm30f60ga | IKCM30F60GA | 1 |  | 726-IKCM30F60GDXKMA1 | https://pt.aliexpress.com/item/32854641564.html | 10.36 | 10.36
CAPACITOR_dcbus |  | *3 | Snubber_cap_0.47uF | CAPACITOR_dcbus | 1 |  | 3106497 (farnell)
gen_purpose_conn_1x2 |  | +VDC1, -VDC2, U1, V1, W1 | connector1x2_parafuso | gen_purpose_conn_1x2 | 5 | C138464 | 172-2555 (rs) | https://pt.aliexpress.com/item/32800814802.html | 10pcs 0,58 | 0.58
 | 10uF 50V | C1, C2, C3, C11, C18, C19, C26 | CAPC_1206 | Capacitor SMD | 7 | C13585 | 963-UMK316BBJ106ML-T | https://pt.aliexpress.com/item/32830755495.html | 100pcs 1,54 | 1.54
cap | 10uF 50V TANT | C4, C5, C6, C7, C8, C9, C10, C24, C25 | CAPC_2917 | tantalum_CAP | 9 | C224948 | 80-T491D106K050AT | https://pt.aliexpress.com/item/32371133579.html | 10pcs 1,14 | 1.14
 | 10nF | C12, C13, C14, C15, C16, C17, C27, C28, C29, C30 | CAPC_0805 | Capacitor SMD | 10 | C83170 | 603-CC805KRX7R9BB103 | https://pt.aliexpress.com/item/33046583537.html | 100pcs 0,72 | 0.72
 |  | C20, C21, C22, C23 | Capacitor_DCBUS | CAPACITOR_dcbus | 4 |  | 661-ESMR451N471MR40S | https://pt.aliexpress.com/item/32862387277.html | 2pcs 7,24 | 14.48
Capacitor SMD | 10uF | C31, C32, C35 | CAPC_0805 | Capacitor SMD | 3 | C337995
Capacitor SMD | 1uF | C33, C34 | CAPC_0805 | Capacitor SMD | 2 | C282734
 |  | CC1, CC2, CC3 | CC6303_SOP8 | Current_Sensor_cc6303 | 3 |  | 630-ACHS-7123-000E | https://pt.aliexpress.com/item/32822774478.html | 0.91 | 2.73
Diode | Default Diode | D1, D2, D3 | Diode_th | Diode | 3 |  |  | https://pt.aliexpress.com/item/4000022215376.html | 10pcs 0,17 | 0.17
Header 3 | Header, 3 pin | P1, P2, P3, P4, P5, P6, P7, P8 | HDR1X3 | Header 3 | 8 |  |  | https://pt.aliexpress.com/item/32896225776.html | 5pcs 4,01 | 4.01
Resistor | Resistor | R1, R2, R3, R4, R5, R6, R10, R11, R12, R13, R14, R15, R16, R17 | RESC_0805 | Resistor | 14
Resistor | Current sense resistor | R7, R8, R9 | RESC6432X09M | Resistor | 3 |  | 2828259 (farnell) | https://pt.aliexpress.com/item/32284883972.html | 20pcs 4,73 | 4.73
Resistor | 30K | R18, R19, R20, R21, R24, R25, R26, R27 | RESC_0805 | Resistor | 8 | C40087 |  | https://pt.aliexpress.com/item/32663193024.html | 0.5 | 0.5
R_MEAS | 150R | R22, R23 | RESC_0805 | Resistor | 2 | C115423 |  | https://pt.aliexpress.com/item/32817221342.html | 100pcs 0,65 | 0.65
Resistor | 7K5 |  | RESC_0805 | Resistor | 0 | C294739 |  | https://pt.aliexpress.com/item/32881824216.html | 100pcs 0,80 | 0.8
DC/DC_ISO | DC/DC_ISO | U2 | DC/DC_ISO | DC/DC_ISO | 1 | C98815 | 919-RFB-0505S | https://pt.aliexpress.com/item/33044998237.html | 2pcs 2,76 | 5.52
AMC1200 |  | U3 | SOIC8 | AMC1200 | 1 | C79905 | 595-AMC1200BDWVR | https://pt.aliexpress.com/item/33051365735.html | 1.19 | 4.76
 |  |  |  |  |  |  |  |  |  | 52.69 | 25.2
 | 400V: 30K + MEAS 150R
 | 530V: 100k + MEAS 250R
 |  |  |  |  |  | V | 530 | 0.00175 | 5mA
 |  |  |  |  |  | P | 0.1 | 302857.1429 | Rtotal
 |  |  |  |  |  | I | 1 | 0.9275
 |  |  |  |  |  | #R | 9.275
 |  |  |  |  |  | R | 32653.06122 | 0.25 | 250mV
 |  |  |  |  |  |  |  | 142.8571429
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

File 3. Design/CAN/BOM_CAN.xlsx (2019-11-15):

fornecedor | VPN | Description | Quantity | price | price total | Column1
MOUSER | 77-VJ0805A150FXACBC | Capacitores de cerâmica multicamada MLCC - SMD/SMT 0805 15pF 50volts C0G 1% | 10 | 0.189 € | 1.89 €
MOUSER | 81-GCM21BR71H105KA3L | Capacitores de cerâmica multicamada MLCC - SMD/SMT 0805 1uF 50volts X7R 10% | 20 | 0.167 € | 3.34 €
MOUSER | 581-08055C104J | Capacitores de cerâmica multicamada MLCC - SMD/SMT 50V .1uF X7R 0805 5% Tol | 20 | 0.021 € | 0.42 €
MOUSER | 710-885012207066 | Capacitores de cerâmica multicamada MLCC - SMD/SMT WCAP-CSGP 10000pF 0805 10% 25V MLCC | 20 | 0.072 € | 1.44 €
MOUSER | 710-61500814221 | Conectores modulares/Conectores de Ethernet WR-MJ Feml Shielded 8P8C Horztl Tab Down | 9 | 2.160 € | 19.44 €
MOUSER | 530-3SP370808SM2A264 | Conectores modulares/Conectores de Ethernet RJ45 Connector | 10 | 0.795 € | 7.95 €
MOUSER | 595-ISO1050DUBR | Isoladores digitais Iso 5V CAN Xcvr | 10 | 3.650 € | 36.50 €
MOUSER | 603-RC0805FR-0749R9L | Resistores de Filme Espesso - SMD 49.9 OHM 1% | 10 | 0.082 € | 0.82 €
MOUSER | 660-RK73B2ATTDD221J | Resistores de Filme Espesso - SMD 220 OHM 5% | 10 | 0.016 € | 0.16 €
MOUSER | 603-RT0805FRE07470RL | Resistores de Filme Fino - SMD 1/8W 470 ohm 1% 50ppm | 10 | 0.052 € | 0.52 €
MOUSER | 604-APT2012SRCPRV | LEDs padrão - SMD RED WATER CLEAR | 10 | 0.081 € | 0.81 €
MOUSER | 855-M20-7832046 | Distribuidores e Alojamento de Fios 20+20 DIL VERTICAL SOCKET TIN | 8 | 2.530 € | 20.24 €
MOUSER | 576-SM24CANB-02HTG | Supressores de ESD / Diodos TVS 500W 24V 2 CH ESD PROT | 1 | 0.385 € | 0.39 €
MOUSER | 810-C2012X7R2E472MAE | Capacitores de cerâmica multicamada MLCC - SMD/SMT SOFT 0805 250V4700pF X7R 20% T: 0.85mm | 2 | 0.221 € | 0.44 €
MOUSER | 81-GRM319R61E106KA2D | Capacitores de cerâmica multicamada MLCC - SMD/SMT 1206 X5R 25V 10uF (CLC) | 2 | 0.170 € | 0.34 €
MOUSER | 660-RK73H2ATTD59R0F | Resistores de Filme Espesso - SMD 1/4W 59 OHM 1% | 4 | 0.111 € | 0.44 €
MOUSER | 71-CRCW08051K50FKEAH | Resistores de Filme Espesso - SMD 1/2watt 1.5Kohms 1% High Power AEC-Q200 | 1 | 0.143 € | 0.14 €
MOUSER | 863-MMSD914T1G | Diodos - Fins gerais, energia, comutação 100V 200mA | 1 | 0.188 € | 0.19 €
MOUSER | 652-SF-1206F050-2 | Fusíveis de montagem em superfícies 0.50A Fast Blow SinglFuse | 1 | 0.568 € | 0.57 €
MOUSER | 651-1830606 | Blocos de terminais plugáveis 3 Pos 3.81mm pitch Through Hole Header | 1 | 2.660 € | 2.66 €
MOUSER | 651-1828359 | Blocos de terminais plugáveis 3 Pos 3.81mm pitch Plug 28-16 AWG Screw | 1 | 2.870 € | 2.87 €
MOUSER | 490-PCN2-S24-S5-S | Conversores CC/CC com isolação 21.6-26.4Vin 5Vout 400mA 2W Iso SIP | 1 | 4.580 € | 4.58 €
MOUSER | 815-AIMC-0805-5N6ST | Indutores fixos 5.6nH, 400mA Tol.=+/-.3nH | 1 | 0.098 € | 0.10 € | 106.248 €
FARNELL | 1675755 | MC34483 - Connector Housing, MC34 Series, Receptacle, 3 Ways, 2.54 mm, 2218T Crimp Contacts | 100 | 0.028 € | 2.75 €
FARNELL | 1675765 | MC34631 - Wire-To-Board Connector, Vertical, 2.54 mm, 3 Contacts, Header, MC34 Series, Through Hole, 1 Rows | 100 | 0.029 € | 2.91 €
RS | 467-598 | Contacto de terminal de crimpado Molex 08-50-0032, KK, 4809, Hembra, Crimpado, Revestimiento de Estaño | 200 | 0.078 € | 15.60 €
RS | 896-6696 | Bloque de terminal PCB, paso5mm 2 Contacto Macho Recta Bloque de terminales PCB, montaje: Montaje en PCB | 20 | 0.240 € | 4.80 €
MOUSER | 595-AMC1200BDWVR | Amplificadores de isolamento 4kV peak Iso Amp | 11 | 4.150 € | 45.65 €
FARNELL | 2443552 | KIT_XMC45_RELAX_LITE_V1 - Evaluation Board, XMC4500 MCU, Detachable On-Board Debugger, USB Powered | 2 | 11.400 € | 22.80 €
RS | 674-2369 | Conector hembra para PCB ASSMANN WSW Recta 40 pines 2 filas paso 2.54mm Montaje Orificio Pasante | 5 | 1.686 € | 8.43 €
 |  |  |  | TOTAL | 209.19 €

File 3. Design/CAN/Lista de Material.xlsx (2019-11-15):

FN
 | Bill of Materials
 | Type Designation: | POWER FLOW
 | PCB Number: | -----
 | Creation Date: | 2019-11-12 | 17:39:36
 | C.C. | 1
 | Designation | Part Description | Price per unit € | Quantity | Price | Seller | Seller reference | Link | Note
 | Shield Can XMC
 | SM24CANB-02HTG | Supressores de ESD / Diodos TVS 500W 24V 2 CH ESD PROT | 0.385 | 1 | 0.385 | Mouser | 576-SM24CANB-02HTG | https://pt.mouser.com/ProductDetail/Littelfuse/SM24CANB-02HTG?qs=bWsWnctWn1wbKmCYlcUmHw%3d%3d | Opt
 | 15 pF | Capacitores de cerâmica multicamada MLCC - SMD/SMT 0805 15pF 50volts C0G 1% | 0.189 | 1 | 0.189 | Mouser | 77-VJ0805A150FXACBC | https://pt.mouser.com/ProductDetail/Vishay-Vitramon/VJ0805A150FXACW1BC
 | 1uF | Capacitores de cerâmica multicamada MLCC - SMD/SMT 0805 1uF 50volts X7R 10% | 0.167 | 2 | 0.334 | Mouser | 81-GCM21BR71H105KA3L | http://pt.mouser.com/ProductDetail/Murata-Electronics/GCM21BR71H105KA03L/
 | 100nF | Capacitores de cerâmica multicamada MLCC - SMD/SMT 50V .1uF X7R 0805 5% Tol | 0.021 | 2 | 0.042 | Mouser | 581-08055C104J | http://pt.mouser.com/ProductDetail/AVX/08055C104JAT2A/
 | 10 nF | Capacitores de cerâmica multicamada MLCC - SMD/SMT WCAP-CSGP 10000pF 0805 10% 25V MLCC | 0.072 | 2 | 0.144 | Mouser | 710-885012207066 | http://pt.mouser.com/ProductDetail/Wurth-Electronics/885012207066/
 | RJ45 (Female) | Conectores modulares/Conectores de Ethernet WR-MJ Feml Shielded 8P8C Horztl Tab Down | 2.16 | 1 | 2.16 | Mouser | 710-61500814221 | https://pt.mouser.com/ProductDetail/Wurth-Electronics/61500814221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
 | RJ45 (Male) | Conectores modulares/Conectores de Ethernet RJ45 Connector | 0.795 | 2 | 1.59 | Mouser | 530-3SP370808SM2A264 | https://pt.mouser.com/ProductDetail/Stewart-Connector-Bel/943-SP-370808SM2-A264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
 | Transceiver | Isoladores digitais Iso 5V CAN Xcvr | 3.65 | 1 | 3.65 | Mouser | 595-ISO1050DUBR | https://pt.mouser.com/ProductDetail/Texas-Instruments/ISO1050DUBR
 | 49.9 Ohm | Resistores de Filme Espesso - SMD 49.9 OHM 1% | 0.082 | 1 | 0.082 | Mouser | 603-RC0805FR-0749R9L | https://pt.mouser.com/ProductDetail/Yageo/RC0805FR-0749R9L?qs=sGAEpiMZZMu61qfTUdNhG5eFuApKbqVd1WlkKcG2JaI%3d
 | 59 Ohm | Resistores de Filme Espesso - SMD 1/4W 59 OHM 1% | 0.111 | 1 | 0.111 | Mouser | 660-RK73H2ATTD59R0F | https://pt.mouser.com/ProductDetail/KOA-Speer/RK73H2ATTD59R0F?qs=OcPyO5%252bjbWlHNMZtTXTMBw%3d%3d | opt
 | 220 Ohm | Resistores de Filme Espesso - SMD 220 OHM 5% | 0.016 | 1 | 0.016 | Mouser | 660-RK73B2ATTDD221J | http://pt.mouser.com/ProductDetail/KOA-Speer/RK73B2ATTDD221J/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
 | 330 Ohm | Resistores de Filme Espesso - SMD 1/4watts 330ohms 5 | 0.361 | 2 | 0.722 | Mouser | 660-RK73B2ATTD331J | https://eu.mouser.com/ProductDetail/KOA-Speer/RK73B2ATTD331J?qs=sGAEpiMZZMu61qfTUdNhG7Y4Xn1xytrntpWPL40Rj4I%3d | opt
 | 470 Ohm | Resistores de Filme Fino - SMD 1/8W 470 ohm 1% 50ppm | 0.052 | 1 | 0.052 | Mouser | 603-RT0805FRE07470RL | http://pt.mouser.com/ProductDetail/Yageo/RT0805FRE07470RL/?qs=sGAEpiMZZMu61qfTUdNhG7XKrGAE6fxHsvRUjrIFZAo%3d
 | Led | LEDs padrão - SMD RED WATER CLEAR | 0.081 | 2 | 0.162 | Mouser | 604-APT2012SRCPRV | http://pt.mouser.com/ProductDetail/Kingbright/APT2012SRCPRV/?qs=sGAEpiMZZMseGfSY3csMkeytxqHAv00Ao5UbNG5ZWqg%3d
 | Headers | Distribuidores e Alojamento de Fios 20+20 DIL VERTICAL SOCKET TIN | 2.53 | 2 | 5.06 | Mouser | 855-M20-7832046 | https://pt.mouser.com/ProductDetail/Harwin/M20-7832046
 | CAN BUS
 | SM24CANB-02HTG | Supressores de ESD / Diodos TVS 500W 24V 2 CH ESD PROT | 0.385 | 1 | 0.385 | Mouser | 576-SM24CANB-02HTG | https://pt.mouser.com/ProductDetail/Littelfuse/SM24CANB-02HTG?qs=bWsWnctWn1wbKmCYlcUmHw%3d%3d
 | 4,7 nF | Capacitores de cerâmica multicamada MLCC - SMD/SMT SOFT 0805 250V4700pF X7R 20% T: 0.85mm | 0.221 | 2 | 0.442 | Mouser | 810-C2012X7R2E472MAE | https://pt.mouser.com/ProductDetail/TDK/C2012X7R2E472M085AE
 | 10uF | Capacitores de cerâmica multicamada MLCC - SMD/SMT 1206 X5R 25V 10uF (CLC) | 0.17 | 2 | 0.34 | Mouser | 81-GRM319R61E106KA2D | http://pt.mouser.com/ProductDetail/Murata-Electronics/GRM319R61E106KA12D/
 | RJ45 (Female) | Conectores modulares/Conectores de Ethernet WR-MJ Feml Shielded 8P8C Horztl Tab Down | 2.16 | 6 | 12.96 | Mouser | 710-61500814221 | https://pt.mouser.com/ProductDetail/Wurth-Electronics/61500814221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
 | 59 Ohm | Resistores de Filme Espesso - SMD 1/4W 59 OHM 1% | 0.111 | 4 | 0.444 | Mouser | 660-RK73H2ATTD59R0F | https://pt.mouser.com/ProductDetail/KOA-Speer/RK73H2ATTD59R0F?qs=OcPyO5%252bjbWlHNMZtTXTMBw%3d%3d
 | Led | LEDs padrão - SMD RED WATER CLEAR | 0.081 | 1 | 0.081 | Mouser | 604-APT2012SRCPRV | http://pt.mouser.com/ProductDetail/Kingbright/APT2012SRCPRV/?qs=sGAEpiMZZMseGfSY3csMkeytxqHAv00Ao5UbNG5ZWqg%3d
 | 1k5 Ohm | Resistores de Filme Espesso - SMD 1/2watt 1.5Kohms 1% High Power AEC-Q200 | 0.143 | 1 | 0.143 | Mouser | 71-CRCW08051K50FKEAH | http://pt.mouser.com/ProductDetail/Vishay/CRCW08051K50FKEAHP/
 | Díodo | Diodos - Fins gerais, energia, comutação 100V 200mA | 0.188 | 1 | 0.188 | Mouser | 863-MMSD914T1G | http://pt.mouser.com/Search/ProductDetail.aspx
 | fusível | Fusíveis de montagem em superfícies 0.50A Fast Blow SinglFuse | 0.568 | 1 | 0.568 | Mouser | 652-SF-1206F050-2 | http://pt.mouser.com/Search/ProductDetail.aspx
 | Connector 24V (Male) | Blocos de terminais plugáveis 3 Pos 3.81mm pitch Through Hole Header | 2.66 | 1 | 2.66 | Mouser | 651-1830606 | https://pt.mouser.com/ProductDetail/Phoenix-Contact/1830606?qs=sGAEpiMZZMsDddcp1dBDJOrXMrFmZFLlA6iEiURh5ug%3d
 | Connector 24V (Female) | Blocos de terminais plugáveis 3 Pos 3.81mm pitch Plug 28-16 AWG Screw | 2.87 | 1 | 2.87 | Mouser | 651-1828359 | https://pt.mouser.com/ProductDetail/Phoenix-Contact/1828359
 | cc-cc 24 to 5 | Conversores CC/CC com isolação 21.6-26.4Vin 5Vout 400mA 2W Iso SIP | 4.58 | 1 | 4.58 | Mouser | 490-PCN2-S24-S5-S | https://pt.mouser.com/ProductDetail/CUI/PCN2-S24-S5-S
 | coil | Indutores fixos 5.6nH, 400mA Tol.=+/-.3nH | 0.098 | 1 | 0.098 | Mouser | 815-AIMC-0805-5N6ST | https://pt.mouser.com/ProductDetail/ABRACON/AIMC-0805-5N6S-T?qs=1vO2EIVe%252bY5QJS8%2fx1Rfvw%3d%3d

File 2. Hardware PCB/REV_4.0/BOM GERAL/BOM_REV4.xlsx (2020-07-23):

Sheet: BOM REV4 (2)
Comment | Description | Designator | Footprint | LibRef | Quantity | Board | RS VPN | Farnell VPN | Mouser VPN | encomendar | PCDIGA VPN | price | price REV4 | comentários p/ RUI
C 10nF 0805 MLCC 50V X7R | Capacitores de cerâmica multicamada MLCC - SMD/SMT 10nF 50V X7R 10% | C19, C20, C21, C22 | CAPC_0805 | Capacitor SMD | 4 | inversor |  |  | 603-CC805KRX7R9BB103 | 20 |  | 0,099 | 1.98 €
C 10uF 1206 MLCC 50V X5R | Capacitores de cerâmica multicamada MLCC - SMD/SMT 1206 50V 10uF 20% X5R | C1, C2, C3, C4, C5, C6, C7, C8, C9, C10, C11, C12 | CAPC_1206 | Capacitor SMD | 12 | middlePCB |  |  | 963-UMK316BBJ106ML-T | 60 |  | 0,31 | 18.60 €
C 10uF 2917 TANT 50V | Condensadores de tântalo - revestimento sólido de SMD 50V 10uF 10% ESR=0.8Ohms | C4, C5, C6, C7, C8, C9, C16, C17, C24 | CAPC_2917 | tantalum_CAP | 9 | inversor |  | 1692396 | 80-T491D106K050AT | 20 |  | 2.82 € | 56.40 € | só tem stock farnell
C 1nF 0805 MLCC 50V X7R | Capacitores de cerâmica multicamada MLCC - SMD/SMT WCAP-CSGP 1000pF 0805 10% 50V MLCC | C10, C11, C12, C13, C14, C15 | CAPC_0805 | Capacitor SMD | 6 | inversor |  |  | 710-885012207086 | 30 |  | 0,08 | 2.40 €
C 33nF MLCC 1812 X7R 630V | Multilayer Ceramic Capacitors MLCC - SMD/SMT 1812 630V 33nF 5% SOFT 2.00mm |  |  | 810-C4532C0G2J333J20 | 10 | inversor |  |  | 810-C4532C0G2J333J20 | 50 |  | 1.80 € | 90.00 €
C 2uF PPCap TH 630V | Capacitores de película 2.0uF 630volts 10% 37.5mmL/S 1.0mmL/D | C2, C4, C6 | C 8uF PPCap TH 900V | CAPACITOR_dcbus | 3 | Filtro | 137-2363 |  |  | 15 |  | 4.34 € | 65.10 €
C 100uF EleCap TH 550V | Aluminium Electrolytic Capacitors - Snap In 550VDC 100uF 20% PVC STD 6.3mm Term | C_bus1, C_bus2, C_bus3, C_bus4 | Capacitor_DCBUS | CAPACITOR_dcbus | 4 | inversor |  |  | 871-B43541A7107M000 | 20 |  | 6.31 € | 126.20 €
IC AmpIso UNI AMC1311 | Amplificadores de isolamento A 595-AMC1311DWV | U4, U5 | AMC1311 - SOIC8 | AMC1311 | 2 | inversor |  |  | 595-AMC1311DWVR | 10 |  | 5,55 | 55.50 €
IC CC/CC 1W 5V | Conversores CC/CC com isolação 1W 5Vin 5Vout 200mA SIP7 | U3, U6, U7 | DC/DC_ISO | DC/DC_ISO | 4 | controlo+inversor |  |  | 919-RFB-0505S | 20 |  | 1,4 | 28.00 €
IC DC/DC 12V | Conversores CC/CC sem isolação 15-36Vin 12Vout 1.0A VSIP Encapsulated | U7 | DC/DC - OKI-78SR-E | DC/DC - R-78E3.3 | 1 | middlePCB |  |  | 580-OKI78SR12/1W36EC | 5 |  | 5,31 | 26.55 €
IC DC/DC 15V ISO | Conversores CC/CC com isolação 6W 18-36Vin 15Vout 400mA DIP24 Iso | U1 | MeanWell SCWNo6 | MEANWELL - SCWN06 | 1 | middlePCB |  |  | 709-SCWN06B-15 | 6 |  | 8,26 | 49.56 €
IC DC/DC 3V3 | Conversores CC/CC sem isolação 3.3V 500MA OUT THRU | U2 | DC/DC - R-78E3.3 | DC/DC - R-78E3.3 | 1 | middlePCB |  |  | 919-R-78E3.3-0.5 | 5 |  | 2,43 | 12.15 €
IC DC/DC 5V | Conversores CC/CC sem isolação 7-36Vin 5Vout 1.5A VSIP Encapsulated | U3, U4 | DC/DC - OKI-78SR-E | DC/DC - R-78E3.3 | 2 | middlePCB |  |  | 580-OK78SR5/1.5W36EC | 10 |  | 5,31 | 53.10 €
IC DIO generic | Diodos - Fins gerais, energia, comutação Hi Conductance Fast | D1, D2, D3 | Diode_th | Diode | 3 | inversor |  |  | 512-1N4148TR | 15 |  | 0,09 | 1.35 €
IC Driver 5A Dual ENA IX4340 | Drivers de portas Dual 5A Gate Driver IC | U5, U8, U10 | SOIC-MIC4126 | Driver - IX4340 | 3 | middlePCB |  |  | 747-IX4340NETR | 15 |  | 0,891 | 13.37 €
IC DUAL MOS DRIVER MIC4127 | Drivers de portas 1.5A Dual High Speed MOSFET Driver with Low Thermal Impedance | U12 | SOIC-MIC4127 | MOS_DRIVER-MIC4127 | 1 | middlePCB |  |  | 998-MIC4127YME-TR | 5 |  | 0.76 € | 3.78 €
IC IGBT IPM IKCM30F60GA | Controladores e drivers de Motor/Movimento/Ignição IFPS MODULES | U2 | ikcm30f60ga | IKCM30F60GA | 1 | inversor |  |  | 726-IKCM30F60GDXKMA1 | 5 |  | 16,25 | 81.25 €
IC ISO SI8660 | Isoladores digitais 1 kV 6-channel digital isolator | U6, U9 | SOIC127P610X155-16N | ISO SI8660 | 2 | middlePCB |  |  | 634-SI8660BA-B-IS1R | 10 |  | 1,82 | 18.20 €
IC LED 1206 | LEDs padrão - SMD GREEN WATER CLEAR | D1, D2, D3, D4 | DIODE_1206 | LED | 4 | middlePCB |  |  | 604-APT3216SGC | 20 |  | 0,387 | 7.74 €
IC Relay 5A 5V 5x20mm | Relés para uso geral 1 form A w/ 5VDC Coil-standard type | U11, U13 | Relay - G6DN | Relay - G6DN | 2 | middlePCB |  |  | 653-G6DN-1A-LDC5 | 10 |  | 1,59 | 15.90 €
IC XMC4500 Relax LITE | " KIT_XMC45_RELAX_LITE_V1 - Evaluation Board, XMC4500 MCU, Detachable On-Board Debugger, USB Powered " | XMC1 | XMC4500 | XMC4500 | 1 | controlo |  | 2443552 |  | 4 |  | 11.91 € | 47.64 €
P 36x2p 2.54 | " KIT_XMC45_RELAX_LITE_V1 - Evaluation Board, XMC4500 MCU, Detachable On-Board Debugger, USB Powered " | XMC1 | XMC4500 | XMC4500 | 2 | controlo | 251-8402 |  |  | 12 |  | 4.48 € | 53.75 €
IND RLS-126 | Indutores fixos Line Inductors for RECOM Power Supply | L1, L2, L3, L4 | Inductor - RLS-126 | Inductor | 4 | middlePCB |  |  | 919-RLS-126-R | 20 |  | 0,549 | 10.98 €
P 20x2p 2.54 | Distribuidores e Alojamento de Fios 20+20 DIL VERTICAL SOCKET TIN |  |  |  | 2 | CAN |  |  | 855-M20-7832046 | 10 |  | 2.53 € | 25.30 €
P 2p 5mm | Bloques de terminales de PCB de perfil estándar RS de 5,0 mm | P7, P8, P9 | connector1x2_parafuso | gen_purpose_conn_1x2 | 16 | controlo | 896-6696 |  |  | 80 |  | 0,24 | 19.20 €
P 4p 2.54 MOL FAN | Distribuidores e Alojamento de Fios 4 PIN HEADER WITH FR R WITH FRICTION LOCK | P12 | HEADER 4p molex | Header 4p molex | 1 | middlePCB |  |  | 538-47053-3000 | 5 |  | 0,405 | 2.03 €
P 8p 2.54 SR DW 3P | Distribuidores e Alojamento de Fios CGrid Hrd SRDW THo le 8ckt | P1 | MOLEX_3p_105431_1103 | Header 3 | 27 | Filtro |  |  | 538-87937-0800 | 135 |  | 0,621 | 83.83 €
P RJ45 FEMALE | Conectores modulares/Conectores de Ethernet WR-MJ Feml Shielded 8P8C Horztl Tab Down |  |  |  | 1 | CAN |  |  | 710-61500814221 | 15 |  | 2.16 € | 32.40 €
P RJ45 MALE | Conectores modulares/Conectores de Ethernet RJ45 Connector |  |  |  | 2 | CAN |  |  | 530-3SP370808SM2A264 | 10 |  | 0.80 € | 7.95 €
R 0 1/8W 0805 | Resistores de Filme Espesso - SMD 1/8Watt 0ohms Commercial Use | R6, R7, R8, R9, R11 | RESC_0805 | Resistor | 5 | middlePCB |  |  | 71-CRCW08050000Z0EAC | 25 |  | 0,09 | 2.25 €
R 0018 3W 6432 1% | MCLRP12JTDRR018 - SMD Current Sense Resistor, 0.018 ohm, LRP Series, 2512 [6432 Metric], 3 W, ± 5%, Metal Strip | R7, R8, R9 | RESC6432X09M | Resistor | 3 | inversor |  | 2828299 |  | 10 |  | 0.25 € | 2.47 €
R 0040 10W 7146 1% | MCLRP12FTWRR039 - SMD Current Sense Resistor, 0.039 ohm, LRP Series, 2512 [6432 Metric], 3 W, ± 1%, Metal Strip | R7, R8, R9 | RESC6432X09M | Resistor | 3 | inversor |  |  | 71-WSHP2818R0400FEA | 20 |  | 1.57 € | 31.40 €
R 10 1/8W 0805 1% | Resistores de Filme Espesso - SMD 1/8Watt 10ohms 1% Commercial Use | R5, R10 | RESC_0805 | Resistor | 2 | middlePCB |  |  | 71-CRCW080510R0FKEAC | 10 |  | 0,09 | 0.90 €
R 2.2 3W TH 5% | Resistores de Fio Enrolado - Orifício de Passagem 5W 10 Ohms 5% | R1, R2, R3 | PWR_RESC_3W | Resistor | 3 | Filtro | 214-2409 |  |  | 15 |  | 0,351 | 5.26 €
R 100 1/8W 0805 1% | Resistores de Filme Espesso - SMD 1/8Watt 100ohms 1% Commercial Use | R1, R2, R3, R4, R5, R6, R10, R12, R13 | RESC_0805 | Resistor | 9 | inversor |  |  | 71-CRCW0805100RFKEAC | 15 |  | 0,09 | 1.35 €
R 150 1/8W 0805 1% | Resistores de Filme Espesso - SMD 1/8watt 150ohms 1% 100ppm | R1 | RESC_0805 | Resistor | 1 | middlePCB |  |  | 71-CRCW0805-150-E3 | 5 |  | 0,09 | 0.45 €
R 1k2 1/8 0805 1% | Resistores de Filme Espesso - SMD 1/8watt 1.2Kohms 1% | R4 | RESC_0805 | Resistor | 1 | middlePCB |  |  | 71-CRCW08051K20FKEA | 5 |  | 0,09 | 0.45 €
R 1k8 1/8W 0805 1% | Resistores de Filme Espesso - SMD ResA-AS 0805 1k8 1% 125mW TC100 | R11 | RESC_0805 | Resistor | 1 | inversor |  |  | 652-CR0805AFX1801EAS | 5 |  | 0,09 | 0.45 €
R 2k7 1/8 0805 1% | Resistores de Filme Espesso - SMD 1/8watt 2.7Kohms 1% 100ppm | R2 | RESC_0805 | Resistor | 1 | middlePCB |  |  | 71-CRCW0805-2.7K-E3 | 5 |  | 0,09 | 0.45 €
R 30k 1/8W 0805 1% | Resistores de Filme Espesso - SMD 0805 30Kohms 1% AEC-Q200 | R20, R21, R22, R23, R26, R27, R28, R29, R30, R31, R32, R33 | RESC_0805 | Resistor | 12 | inversor |  |  | 667-ERJ-6ENF3002V | 10 |  | 0,09 | 0.90 €
R 330 1/4W 0805 5% | Resistores de Filme Espesso - SMD 1/4watts 330ohms 5 |  |  |  | 2 | CAN |  |  | 660-RK73B2ATTD331J | 10 |  | 0.36 € | 3.61 €
R 330 1/8 0805 1% | Resistores de Filme Espesso - SMD 1/8Watt 330ohms 1% Commercial Use | R3 | RESC_0805 | Resistor | 1 | middlePCB |  |  | 71-CRCW0805330RFKEAC | 5 |  | 0,09 | 0.45 €
R 3K 1/8W 0805 1% | Resistores de Filme Espesso - SMD 1/8watt 3Kohms 1% 100ppm | R14 | RESC_0805 | Resistor | 1 | inversor |  |  | 71-CRCW0805-3K-E3 | 5 |  | 0,09 | 0.45 €
R 3k6 1/8W 0805 1% | Resistores de Filme Espesso - SMD 1/8watt 3.6Kohms 1% | R16 | RESC_0805 | Resistor | 1 | inversor |  |  | 71-CRCW08053K60FKEA | 5 |  | 0,09 | 0.45 €
R 470 1/8W 0805 1% | Resistores de Filme Fino - SMD 1/8W 470 ohm 1% 50ppm |  |  |  | 1 | CAN |  |  | 603-RT0805FRE07470RL | 5 |  | 0.05 € | 0.26 €
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

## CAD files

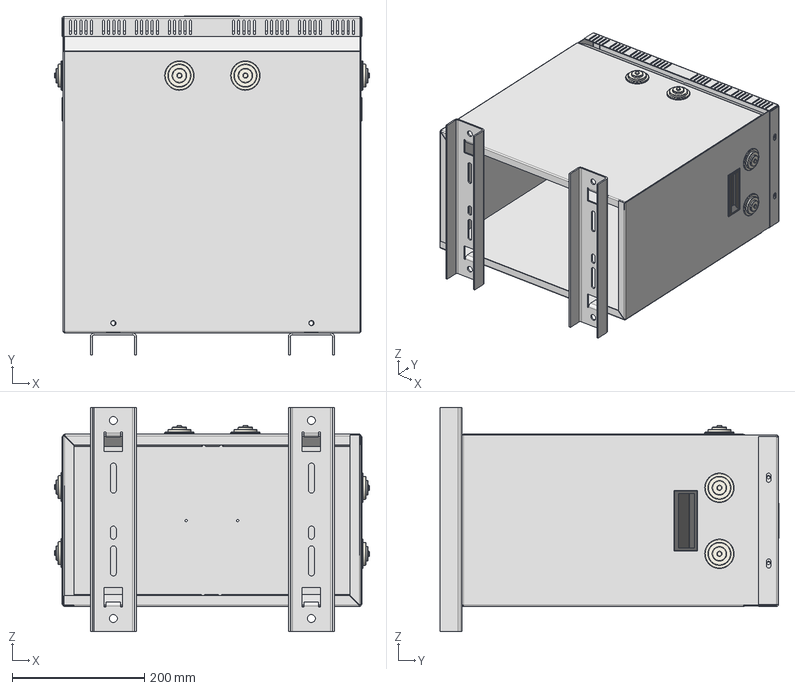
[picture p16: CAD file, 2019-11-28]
3. Design/1p_uG/CADs/PN.NOR.0117-V1.stp
477.2 x 513.0 x 340.0 mm
lateral ca014c23 prensastopas
lateral ca014c23
tapa caj014c23
pie caj014c23 x 2
P2413D x 2
Etiqueta de aluminio pequeña_buena
Pasacables PG29 x 6

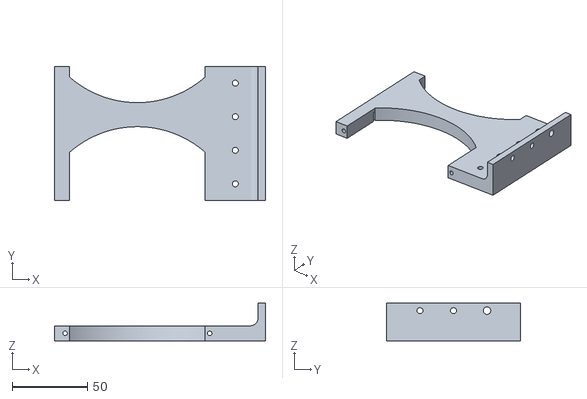
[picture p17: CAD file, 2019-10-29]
3. Design/Desenhos CAD/3d_print_v1/suporte_conversor_trás.STL
140.0 x 89.0 x 25.0

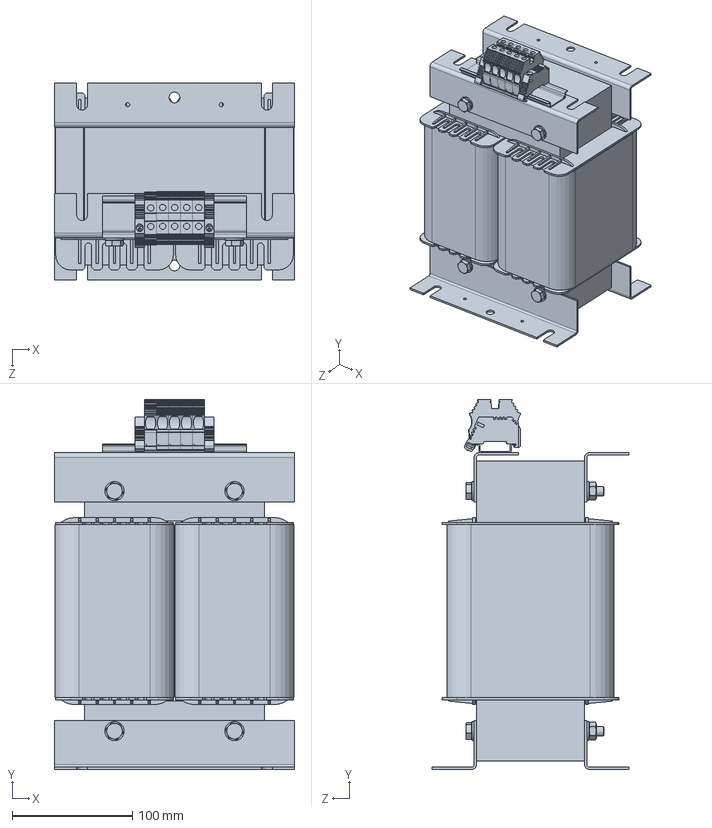
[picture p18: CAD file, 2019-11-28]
3. Design/1p_uG/CADs/PN.NOR.SLDPRT
200.0 x 308.3 x 164.0 mm

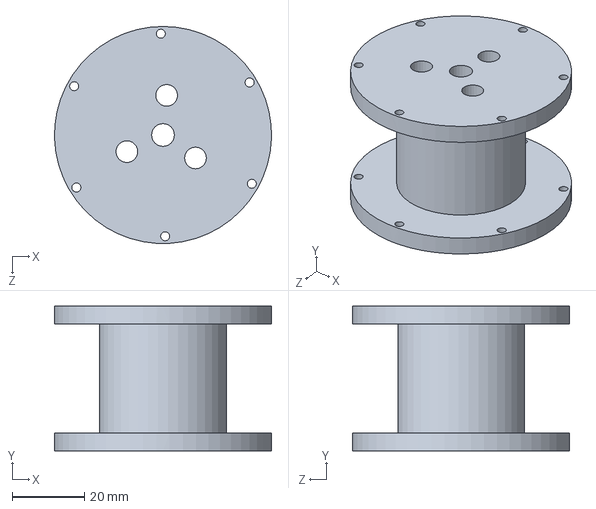
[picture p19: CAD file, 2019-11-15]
3. Design/Desenhos CAD/forma_3d_v3.SLDPRT
60.0 x 40.0 x 60.0 mm

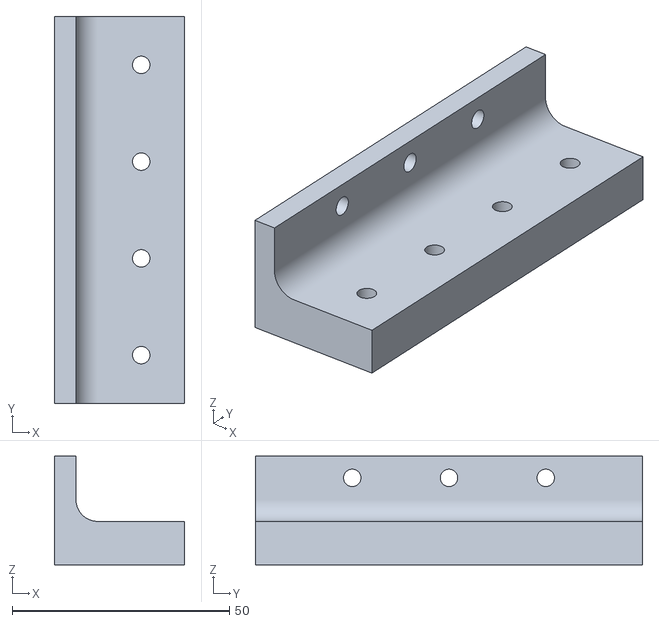
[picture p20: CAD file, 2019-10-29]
3. Design/Desenhos CAD/3d_print_v1/suporte_esquadro.STL
30.0 x 89.0 x 25.0

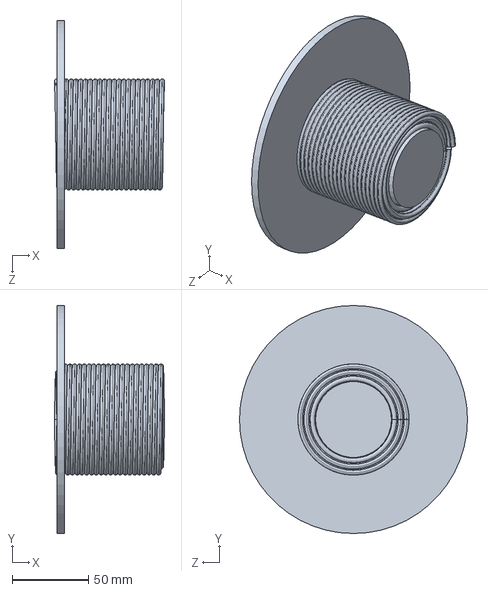
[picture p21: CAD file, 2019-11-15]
3. Design/Desenhos CAD/bobina.SLDPRT
72.4 x 150.0 x 150.0 mm

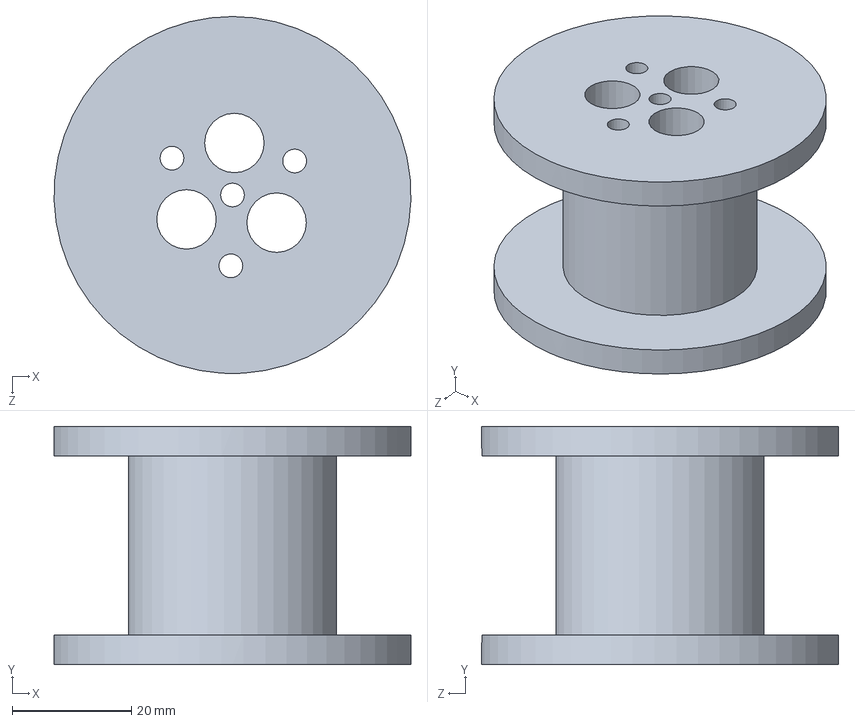
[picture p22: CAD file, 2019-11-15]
3. Design/Desenhos CAD/forma_3d_metade.SLDPRT
60.0 x 40.0 x 60.0 mm

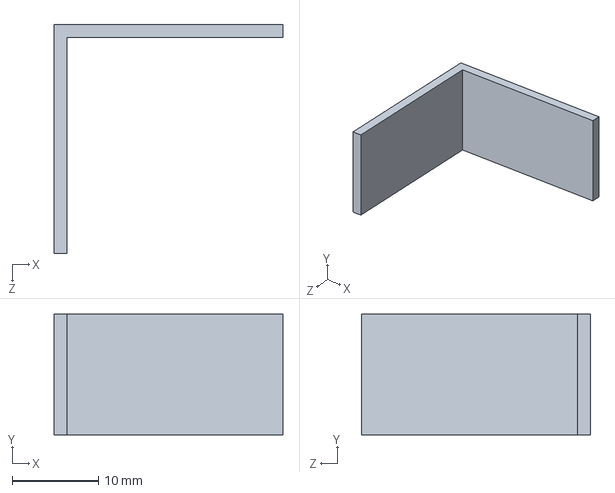
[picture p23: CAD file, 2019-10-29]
3. Design/Desenhos CAD/esquadro.SLDPRT
26.5 x 14.0 x 26.5 mm

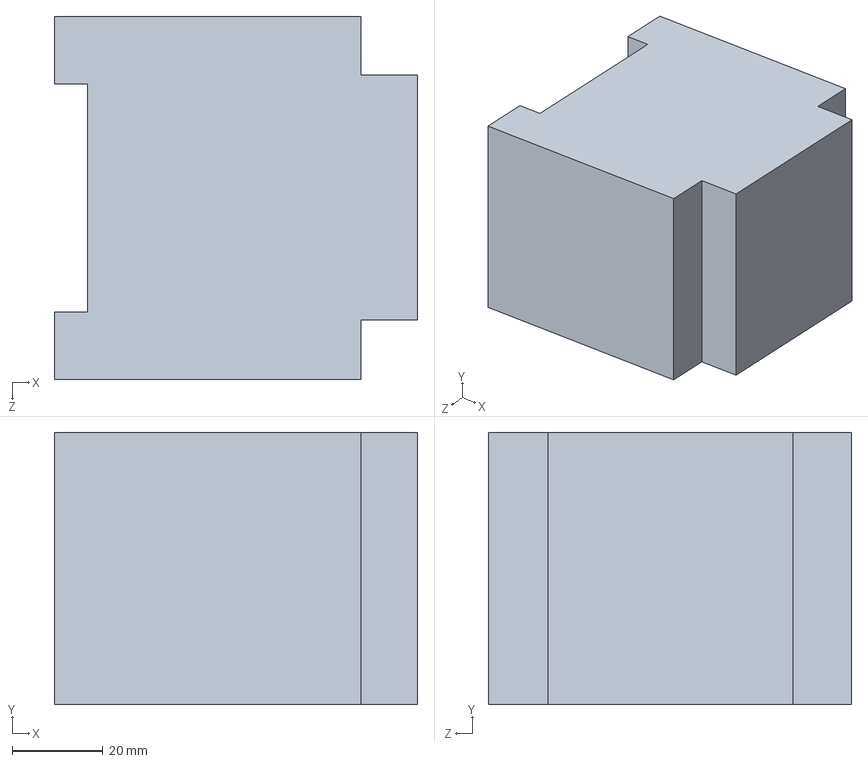
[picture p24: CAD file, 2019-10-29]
3. Design/Desenhos CAD/contactor.SLDPRT
80.0 x 60.0 x 80.0 mm

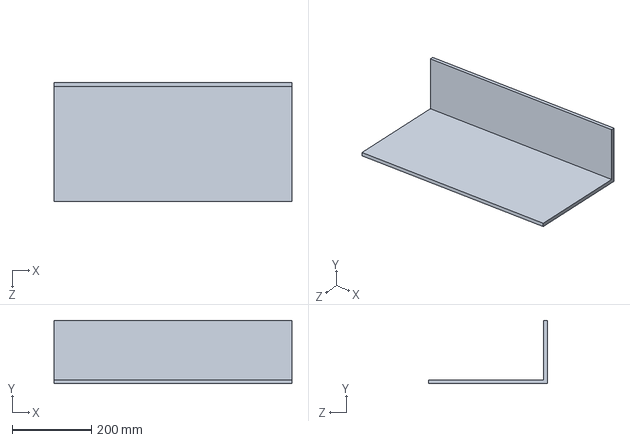
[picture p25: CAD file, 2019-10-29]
3. Design/Desenhos CAD/estrutura_madeira.SLDPRT
600.0 x 160.0 x 300.0 mm

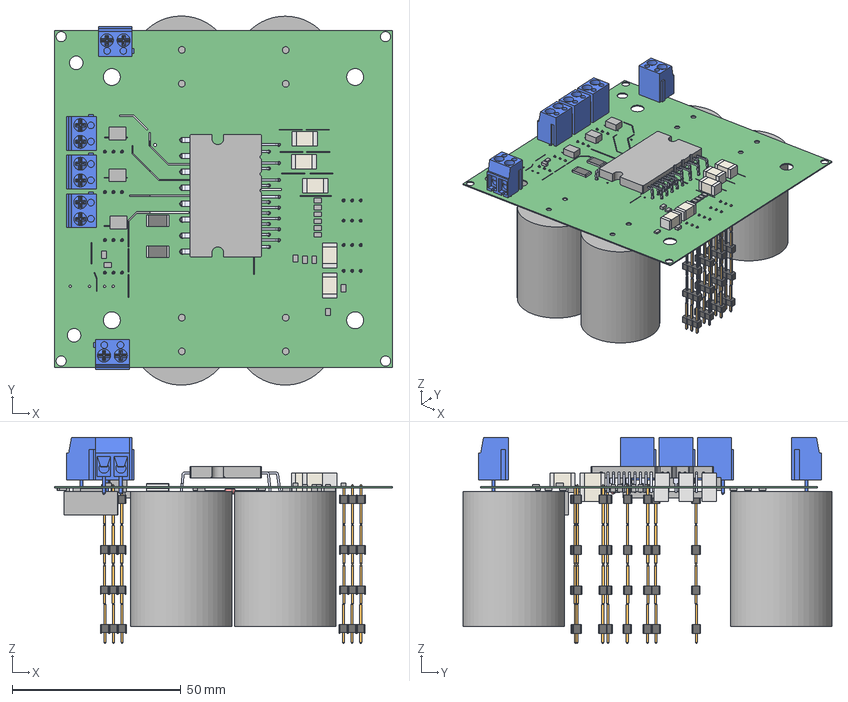
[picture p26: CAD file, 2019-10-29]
3. Design/Desenhos CAD/inversor_rev2.step
100.1 x 109.2 x 61.0 mm
Board
Extruded x 79
zl201-3_p2-54_l7-62_w2-54_h8-89 x 32
SCREW_TERMINAL_BLOCK_5MM x 5
User_Library-Cipos-mini-PCB
Mid_Body x 3
Open_CASCADE_STEP_translator_6.8_1.2.1 x 6
Mark x 3

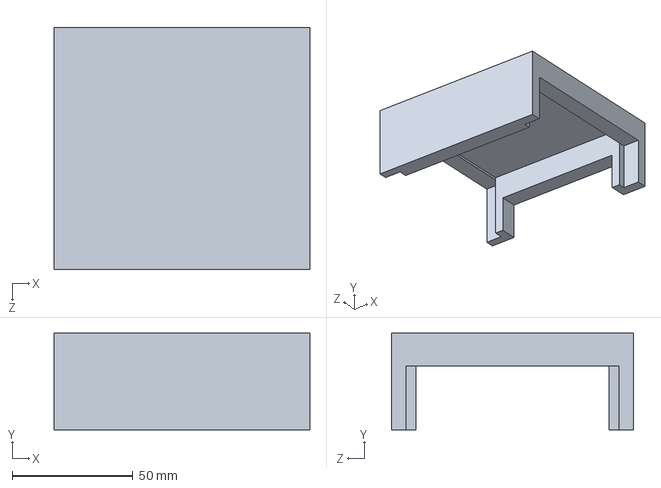
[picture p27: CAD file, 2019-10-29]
3. Design/Desenhos CAD/suporte_topo.SLDPRT
106.0 x 40.0 x 100.0 mm

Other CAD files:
3. Design/Desenhos CAD/3d_print_v1/suporte_conversor_frente.STL
3. Design/1p_uG/CADs/PN.NOR.0102-V1.stp
3. Design/Desenhos CAD/forma_3d.SLDPRT
3. Design/Desenhos CAD/suporte_conversor_frente.SLDPRT
3. Design/Desenhos CAD/suporte_esquadro.SLDPRT
3. Design/Desenhos CAD/suporte_conversor_trás.SLDPRT
2. Hardware PCB/REV_2.0/accets/User Library-Cipos-mini-PCB/User Library-Cipos-mini-PCB.STEP
2. Hardware PCB/REV_2.0/accets/diode-do-35-1.snapshot.15/do35-h_p7_d1-5_l3.igs
2. Hardware PCB/REV_2.0/accets/diode-do-35-1.snapshot.15/do35-h_p7_d1-5_l3.stp
2. Hardware PCB/REV_2.0/accets/diode-do-35-1.snapshot.15/do35_d1-5_l3.igs
2. Hardware PCB/REV_2.0/accets/diode-do-35-1.snapshot.15/do35_d1-5_l3.stp
2. Hardware PCB/REV_2.0/accets/zl201-3_p2-54_l7-62_w2-54_h8-89.stp
2. Hardware PCB/REV_3.0/CAD/87937-0800_stp/879370800.stp
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

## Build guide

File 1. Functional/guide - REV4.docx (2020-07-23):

# 3-PHASE POWER INVERTER

Guide to operate the 3-phase inverter experimental setup
(v.morais@fe.up.pt)

# 1 Features

- The 3-phase 30A@450V power inverter for academic/research purposes;
- This inverter has built-in measurements of AC currents, AC voltages and DC bus voltage;
- The inverter is based on infineon IPM IKCM30F60GA module (a low-cost module, with integrated drivers);
- The control board is based on XMC4500 Relax (lite) kit, a well-known board in UP Laboratory of Power Electronics;

# 2 SCHEMATIC

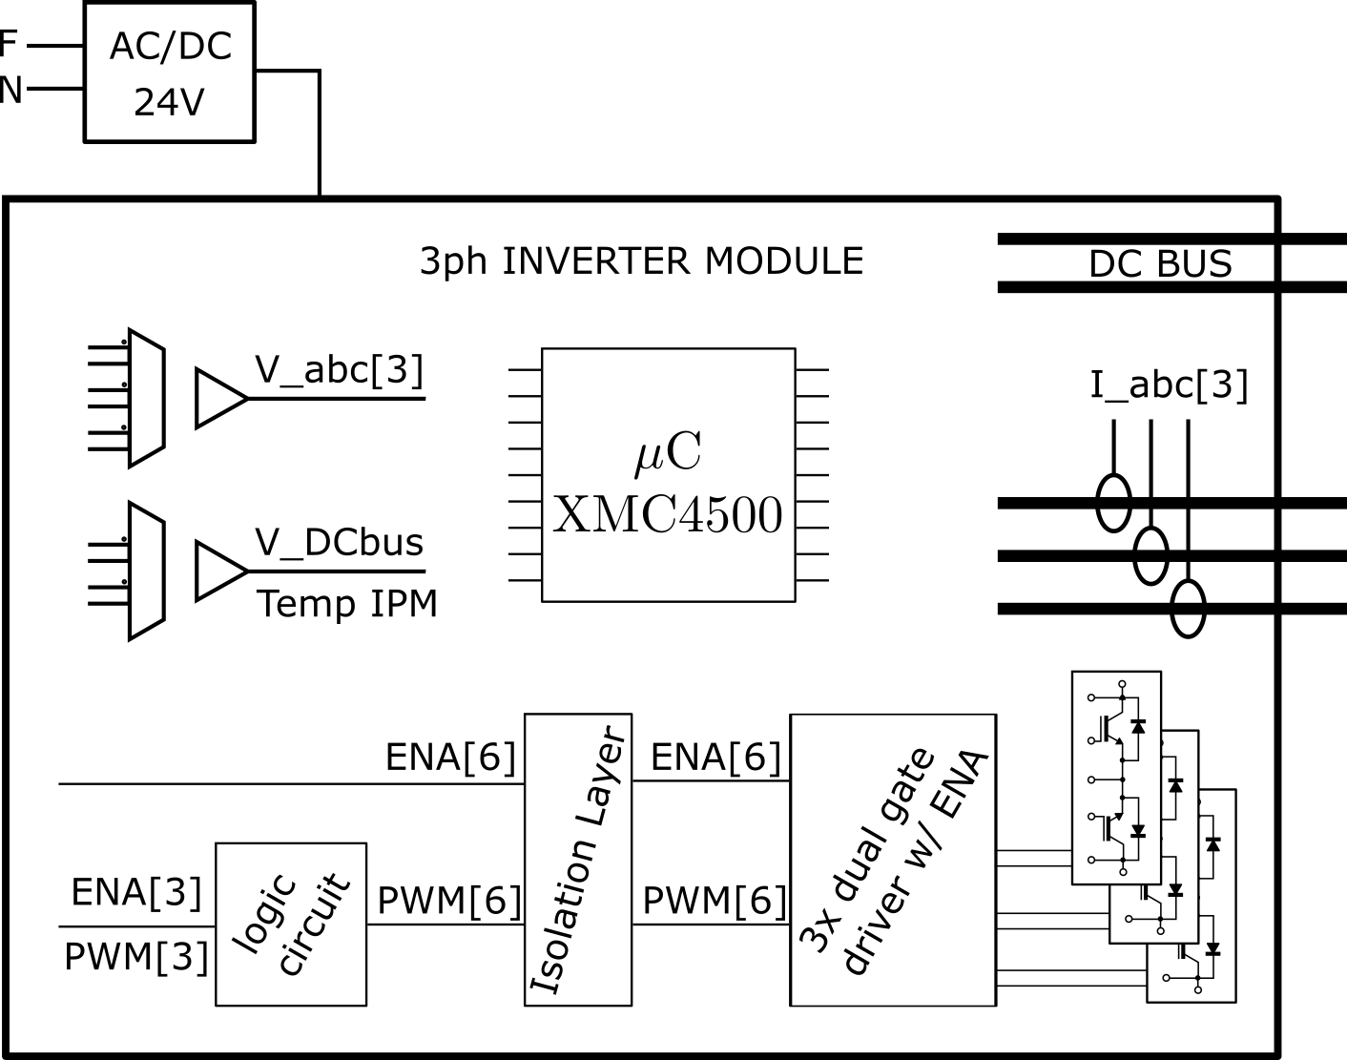
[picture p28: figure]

Figure 1 - general schematic.

# 3 PWM Generation waveforms

The PWM generation implemented in this power inverter module uses the following logic circuit:

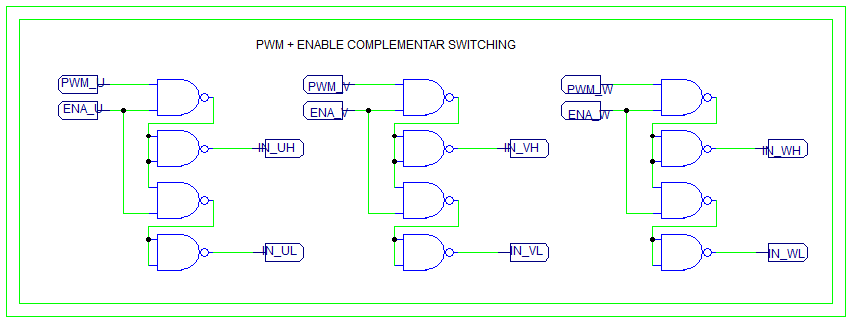
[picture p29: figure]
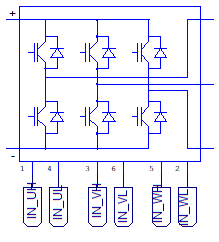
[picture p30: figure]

Figure 2 – Detail of logic circuit for PWM generation.

This arrangement allows the generation of two complementary PWM for each inverter arm. In addition, there is an enable signal for each inverter arm.

These signals pass through an isolation layer, and later though three dual gate drivers, with enable, for each transistor, following:

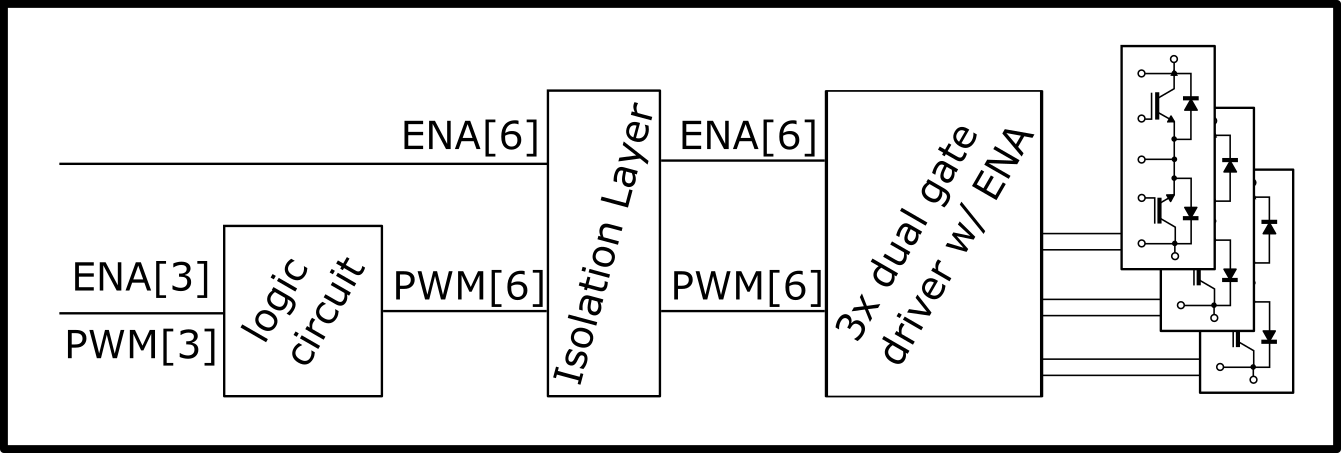
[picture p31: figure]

Figure 3 - General PWM generation.

On the XMC4500 side, the PWM pins are the following:

Functional pin | XMC4500 pin | description
PWM U | P0.4 | Pwm signal
PWM V | P0.6 | Pwm signal
PWM W | P0.5 | Pwm signal
ENA U | P2.6 | Enable arm U
ENA V | P5.2 | Enable arm V
ENA W | P5.0 | Enable arm W
iso_ENA_UH | P0.2 | Enable arm U high side IGBT
iso_ENA_UL | P3.2 | Enable arm U low side IGBT
iso_ENA_VH | P0.11 | Enable arm V high side IGBT
iso_ENA_VL | P3.1 | Enable arm V low side IGBT
iso_ENA_WH | P3.3 | Enable arm W high side IGBT
iso_ENA_WL | P3.0 | Enable arm W low side IGBT

# 4 Acquisition of electric waveforms

This setup has built-in measurements of electric waveforms, specifically three currents (for each of the phases), the DC voltage and three AC isolated voltage measurements.

## 4.1 Current Measurements (three internal measurements)

The current measurement is performed with an isolated hall effect based current sensor, specifically the ACS713ELCTR-20A-T. The maximum value for the AC current sensor is +/- 20A peak.

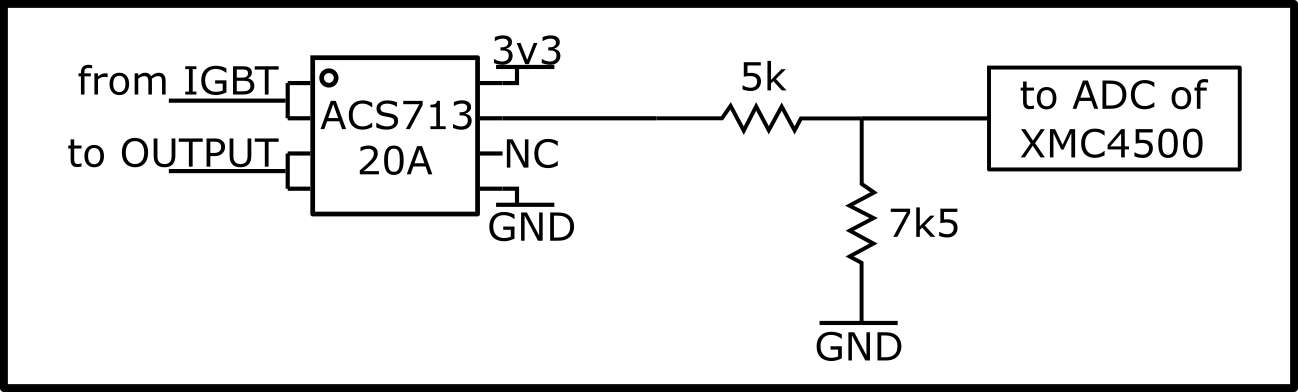
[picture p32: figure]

Figure 4 - Schematic for internal current measurment. NOTE1: the resistors can be removed to reach the maximum scale of the ADCs; NOTE2: for the external measurement, the same circuit is employed, without resistors.

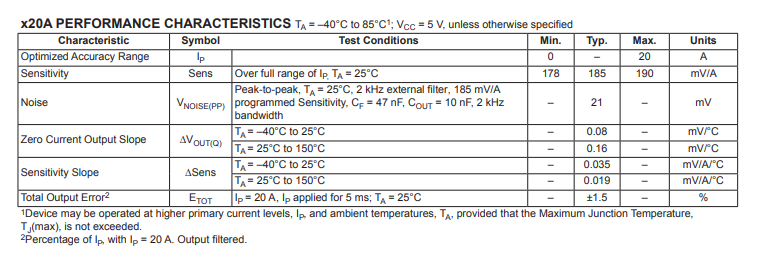
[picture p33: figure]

Figure 5 - Detail of the datasheet

In the provided code, the acquisition is performed at the beginning of the 10 kHz interruption, in the “Update_PWM(void)” function:

/// ADC acquisition - AC Currents

I_abc_adc[0]=ADC_MEASUREMENT_ADV_GetResult(&ADC_MEASUREMENT_2_V2_2);

I_abc_adc[1]=ADC_MEASUREMENT_ADV_GetResult(&ADC_MEASUREMENT_1_V1_4);

I_abc_adc[2]=ADC_MEASUREMENT_ADV_GetResult(&ADC_MEASUREMENT_1_V1_3);

I_abc[0]=(I_abc_adc[0]- (1800.0f + 74.8f)) * 0.022222222f;

I_abc[1]=(I_abc_adc[1]- (1800.0f + 77.0f)) * 0.022179506f;

I_abc[2]=(I_abc_adc[2]- (1800.0f + 70.8f)) * 0.021897810f;

Due to the precision of the resistors in the resistor divider, an offset and gain error occurs. A practical calibration of each sensor is recommended, with the calibration procedures presented in section 6.4.

## 4.2 DC_BUS Voltage Measurement

The DC bus voltage measurement is performed with an isolation amplifier, namely the AMC1311 (http://www.ti.com/product/AMC1311), as illustrated in the following figure:

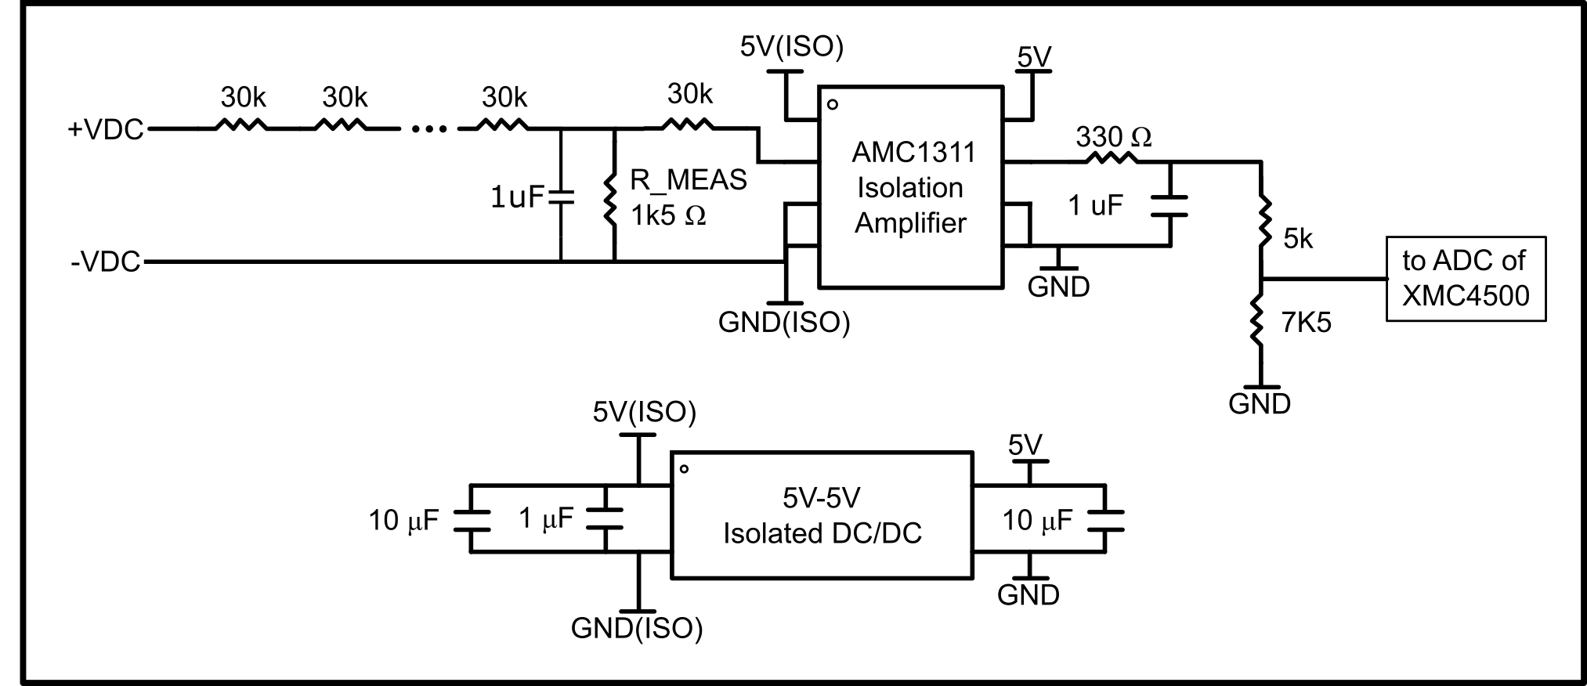
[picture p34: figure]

Figure 6 - Schematic for DC voltage measurement

Similarly, in the provided code, the acquisition is performed at the beginning of the 10 kHz interruption, in the “Update_PWM(void)” function:

/// ADC acquisition – DC_BUS Voltage

V_DC_adc = ADC_MEASUREMENT_ADV_GetResult(&ADC_MEASUREMENT_1_V1_2);

V_DC = (V_DC_adc-(1800.0f + 22.4f)) * -0.58f;

Due to the precision of the resistors, an offset and gain error occurs. A practical calibration of each sensor is recommended, with the calibration procedures presented in section 6.4.

## 4.3 AC Voltage Measurements (Three Measurements)

Similarly to the DC Bus Voltage measurement, AC voltage measurement is performed with an isolation amplifier, as illustrated in the following figure:

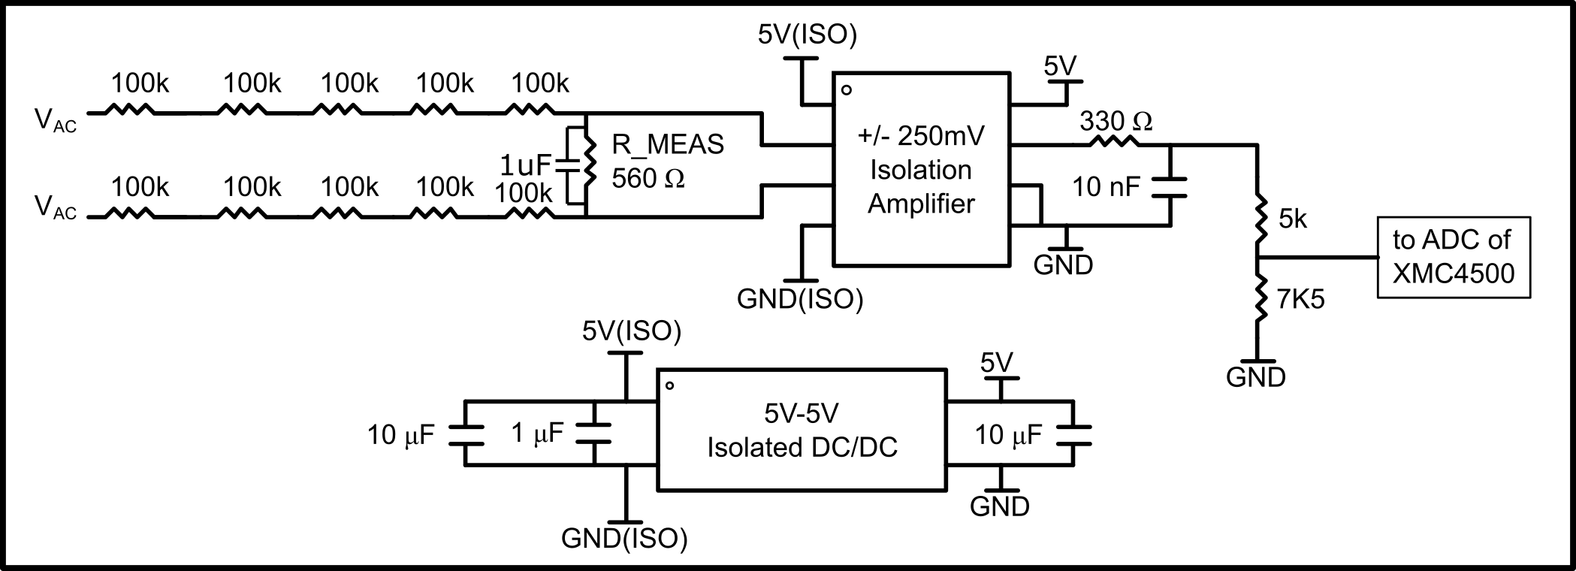
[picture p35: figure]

Figure 7 - Schematic of AC voltage measurement

In the provided code, the acquisition is performed at the beginning of the 10 kHz interruption, in the “Update_PWM(void)” function:

/// ADC acquisition - AC Voltages

V_abc_adc[0]=ADC_MEASUREMENT_ADV_GetResult(&ADC_MEASUREMENT_1_V1_1);

V_abc_adc[1]=ADC_MEASUREMENT_ADV_GetResult(&ADC_MEASUREMENT_2_V2_1);

V_abc_adc[2]=ADC_MEASUREMENT_ADV_GetResult(&ADC_MEASUREMENT_2_V2_3);

V_abc[0]=(V_abc_adc[0]- (1800.0f + 23.92f)) * 0.720f;

V_abc[1]=(V_abc_adc[1]- (1800.0f + 16.50f)) * 0.720f;

V_abc[2]=(V_abc_adc[2]- (1800.0f + 2.930f)) * 0.720f;

Due to the precision of the resistors in the resistor divider, an offset and gain error occurs. A practical calibration of each sensor is recommended, with the calibration procedures presented in section 6.4.

## 4.4 Temperature measurement

Based on the built-in thermistor of IKCM30F60GA IGBT module, the temperature is acquired, with the following code:

float conv_temperature = ADC_MEASUREMENT_ADV_GetResult(&ADC_MEASUREMENT_3_V3_1);

float conv_temp_C =(conv_temperature*conv_temperature*-0.00016973) + //x^2

(conv_temperature*0.69969095) + //x^1

-653.10731030; //x^0

conv_temp_C += 7.0f; //offset compensation (junction temperature)

This is performed with the isolation amplifier AMC1311.

## 4.5 PINOUT

Functional pin | XMC4500 pin | description
Vabc_0 | P14.1 | Voltage AC
Vabc_1 | P14.3 | Voltage AC
Vabc_2 | P14.5 | Voltage AC
Vdc_bus | P14.7 | Voltage DC bus
Temp_IPM | P14.13 | IPM temperature (termistor)
Iabc_1 | P14.8 | Current at phase Iu
Iabc_2 | P14.2 | Current at phase Iv
Iabc_3 | P14.0 | Current at phase Iw
Irst_0 (Flat cable 2) | P15.2 | Current at grid side phase R
Irst_1 (Flat cable 3) | P14.14 | Current at grid side phase S
Irst_2 (Flat cable 4) | P14.12 | Current at grid side phase T
EXTRA (Flat cable 5) | P14.6 | NOT USED
EXTRA (Flat cable 5) | P14.4 | NOT USED

# 5 Version control

V1.0 – preliminary – v.morais@fe.up.pt

V1.1 – added PWM generation details, ADC details and minor updates in the How to use section – v.morais@fe.up.pt

V1.2 – Major revision for REV 4.0 – vmorais@fe.up.pt

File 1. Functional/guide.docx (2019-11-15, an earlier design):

# 3-PHASE POWER INVERTER

Guide to operate the 3-phase inverter experimental setup
(v.morais@fe.up.pt)

# 1 Features

- The 3-phase 30A@450V power inverter for academic/research purposes;
- This inverter has built-in measurements of AC currents, AC voltages and DC bus voltage;
- The inverter is based on infineon IPM IKCM30F60GA module (a low-cost module, with integrated drivers);
- The control board is based on XMC4500 Relax (lite) kit, a well-known board in UP Laboratory of Power Electronics;

# 2 Safety Issues

This module and all electric equipment’s are under dangerous voltages. The operation of this setup may require supervision to avoid injuries as well as destruction of equipment’s.

Next, some advices are listed:

- Keep the “shutdown” button of the DC BUS voltage source easily accessible;
- Always ensure the measurement of the DC bus voltage; A continuous current measurement with an oscilloscope current clamp is recommended.
- Avoid short-circuits with the scope’s ground wire: differential measurements are recommended;
- The isolation transformer is mandatory;
- The heatsink is not grounded. Despite being safe to touch the heatsink it is not recommended. A temperature measurement of the IGBT is available.
- Avoid plug/unplug loads under operation.

# 3 How to use

- SETUP:
  - Download/read IKCM30F60GA datasheets
    - https://www.infineon.com/dgdl/Infineon-IKCM30F60GA-DS-v02_06-EN.pdf?fileId=5546d4624fb7fef2014fcb83cab8790a
  - Download and install last version of DAVE and micrium
    - https://www.infineon.com/cms/en/product/microcontroller/32-bit-industrial-microcontroller-based-on-arm-cortex-m/
    - https://infineoncommunity.com/dave-download_ID645
    - https://infineoncommunity.com/uC-Probe-XMC-software-download_ID712
  - Clone github repository for this 3-phase inverter
    - https://github.com/vitormorais/3phase_inverter
- FIRST RUN (software)
  - Open Dave, import repository:
    - File->Import->General->Existing Projects into Workspace->Select archive file
    - “\3phase_inverter\4. Software_WS\SELE_initialProject.zip”
    - Open main.c;
    - On C/C++ Projects tab, and on SELE_initialProject, right click and “Set active Project”; Then right click and “Build Configurations->Set active->DEBUG”
  - Connect to XMC4500 via USB; click on DEBUG
    - It might ask to create a debug configuration: Double click on “GBD SEGGER JLink Debugging”, then press “Search Project…”, then select the debug binary “SELE_initialProject.elf” and then press DEBUG
    - It should compile and flash the microcontroller; press run button on debug environment.
  - Open micrium file “SELE_micrium.wspx” via DAVE CE workspace
  - If requested, select the SELE_initialProject.elf binary
  - Put in oscilloscope window and press “play” button
  - Now you can control the modulation index, the frequency, etc and monitor certain waveforms
- SETUP HARDWARE
  - Connect to the DC bus a voltage source
    - First use the LAB voltage source (max 30V)
    - Check with the oscilloscope probe the ac voltage of each of the 3phase outputs (with the scope ground connected to the negative side of –VDC_BUS)
      - You should see the PWM at 10 kHz
  - Now, if all PWM are OK, connect a DC power source (isolation transformer + VARIAC + Rectifier)
  - Connect a 3phase load (RL) to the respective inverter outputs
  - Turn on the DC voltage source (with 30V); Check the LOAD current with a current probe: it should be a 50Hz current;
  - Now test the micrium interface with different frequencies, modulation indexes, etc

# 4 SCHEMATIC

# 5 PWM Generation waveforms

The PWM generation implemented in this power inverter module uses the following logic circuit:


This arrangement allows the generation of two complementary PWM for each inverter arm. In addition, there is an enable signal for each inverter arm.

On the XMC4500 side, the PWM pins are the following: P0.5, P0.6 and P0.4; Respectively, the P0.8, P0.12 and P0.2

# 6 Acquisition of electric waveforms

This setup has built-in measurements of electric waveforms, specifically three currents (for each of the phases), the DC voltage and three AC isolated voltage measurements.

## 6.1 Current Measurements (three measurements)

The current measurement is performed with an isolated hall effect based current sensor, specifically the ACHS-7123-000E (https://www.broadcom.com/products/optocouplers/industrial-plastic/other/hall-effect-sensors/achs-7123-000e). The maximum value for the AC current sensor is +/- 30A peak.

In the provided code, the acquisition is performed at the beginning of the 10 kHz interruption, in the “Update_PWM(void)” function:

/// ADC acquisition - AC Currents

I_abc_adc[0]=ADC_MEASUREMENT_ADV_GetResult(&ADC_MEASUREMENT_2_V2_2);

I_abc_adc[1]=ADC_MEASUREMENT_ADV_GetResult(&ADC_MEASUREMENT_1_V1_4);

I_abc_adc[2]=ADC_MEASUREMENT_ADV_GetResult(&ADC_MEASUREMENT_1_V1_3);

I_abc[0]=(I_abc_adc[0]- (1800.0f + 74.8f)) * 0.022222222f;

I_abc[1]=(I_abc_adc[1]- (1800.0f + 77.0f)) * 0.022179506f;

I_abc[2]=(I_abc_adc[2]- (1800.0f + 70.8f)) * 0.021897810f;

Due to the precision of the resistors in the resistor divider, an offset and gain error occurs. A practical calibration of each sensor is recommended, with the calibration procedures presented in section 6.4.

## 6.2 DC_BUS Voltage Measurement

The DC bus voltage measurement is performed with an isolation amplifier, namely the ACM1200 (http://www.ti.com/product/AMC1200), as illustrated in the following figure:

Similarly, in the provided code, the acquisition is performed at the beginning of the 10 kHz interruption, in the “Update_PWM(void)” function:

/// ADC acquisition – DC_BUS Voltage

V_DC_adc = ADC_MEASUREMENT_ADV_GetResult(&ADC_MEASUREMENT_1_V1_2);

V_DC = (V_DC_adc-(1800.0f + 22.4f)) * -0.58f;

Due to the precision of the resistors, an offset and gain error occurs. A practical calibration of each sensor is recommended, with the calibration procedures presented in section 6.4.

## 6.3 AC Voltage Measurements (Three Measurements)

Similarly to the DC Bus Voltage measurement, AC voltage measurement is performed with an isolation amplifier, as illustrated in the following figure:

In the provided code, the acquisition is performed at the beginning of the 10 kHz interruption, in the “Update_PWM(void)” function:

/// ADC acquisition - AC Voltages

V_abc_adc[0]=ADC_MEASUREMENT_ADV_GetResult(&ADC_MEASUREMENT_1_V1_1);

V_abc_adc[1]=ADC_MEASUREMENT_ADV_GetResult(&ADC_MEASUREMENT_2_V2_1);

V_abc_adc[2]=ADC_MEASUREMENT_ADV_GetResult(&ADC_MEASUREMENT_2_V2_3);

V_abc[0]=(V_abc_adc[0]- (1800.0f + 23.92f)) * 0.720f;

V_abc[1]=(V_abc_adc[1]- (1800.0f + 16.50f)) * 0.720f;

V_abc[2]=(V_abc_adc[2]- (1800.0f + 2.930f)) * 0.720f;

Due to the precision of the resistors in the resistor divider, an offset and gain error occurs. A practical calibration of each sensor is recommended, with the calibration procedures presented in section 6.4.

## 6.4 Calibration procedures for the measurements

As visible in the code, the calibration was performed, having the form:

I_abc[k]=(I_abc_adc[k]-OFFSET) * GAIN;

STEP1: set GAIN =1 and OFFSET = 0; program the microcontroller and open the micrium code;

STEP2: obtain the OFFSET, based on the measurement of the RMS value displayed in the oscilloscope interface of the micrium;

STEP3: adjust the program to include the offset. Download and run again the code.

STEP4.1: For the DC voltage, increase the DC bus voltage, and obtain the gain with the formula: Gain = V(real)/V(micrium)

STEP4.2: For the AC voltages, connect an AC voltage with a VARIAC and obtain the gain by comparing the RMS value of micrium and the multimeter;

STEP4.3: For the AC Currents, connect a RL load, enable the PWM, supply the DC bus and measure the current with the oscilloscope; compare the measured value with the displayed value in the micrium; adjust the gain accordingly.

## 6.5 Temperature measurement

Based on the built-in thermistor of IKCM30F60GA IGBT module, the temperature is acquired, with the following code:

float conv_temperature = ADC_MEASUREMENT_ADV_GetResult(&ADC_MEASUREMENT_3_V3_1);

float conv_temp_C =(conv_temperature*conv_temperature*-0.00016973) + //x^2

(conv_temperature*0.69969095) + //x^1

-653.10731030; //x^0

conv_temp_C += 7.0f; //offset compensation (junction temperature)

# 7 Version control

V1.0 – preliminary – v.morais@fe.up.pt

V1.1 – added PWM generation details, ADC details and minor updates in the How to use section – v.morais@fe.up.pt

V1.2 -

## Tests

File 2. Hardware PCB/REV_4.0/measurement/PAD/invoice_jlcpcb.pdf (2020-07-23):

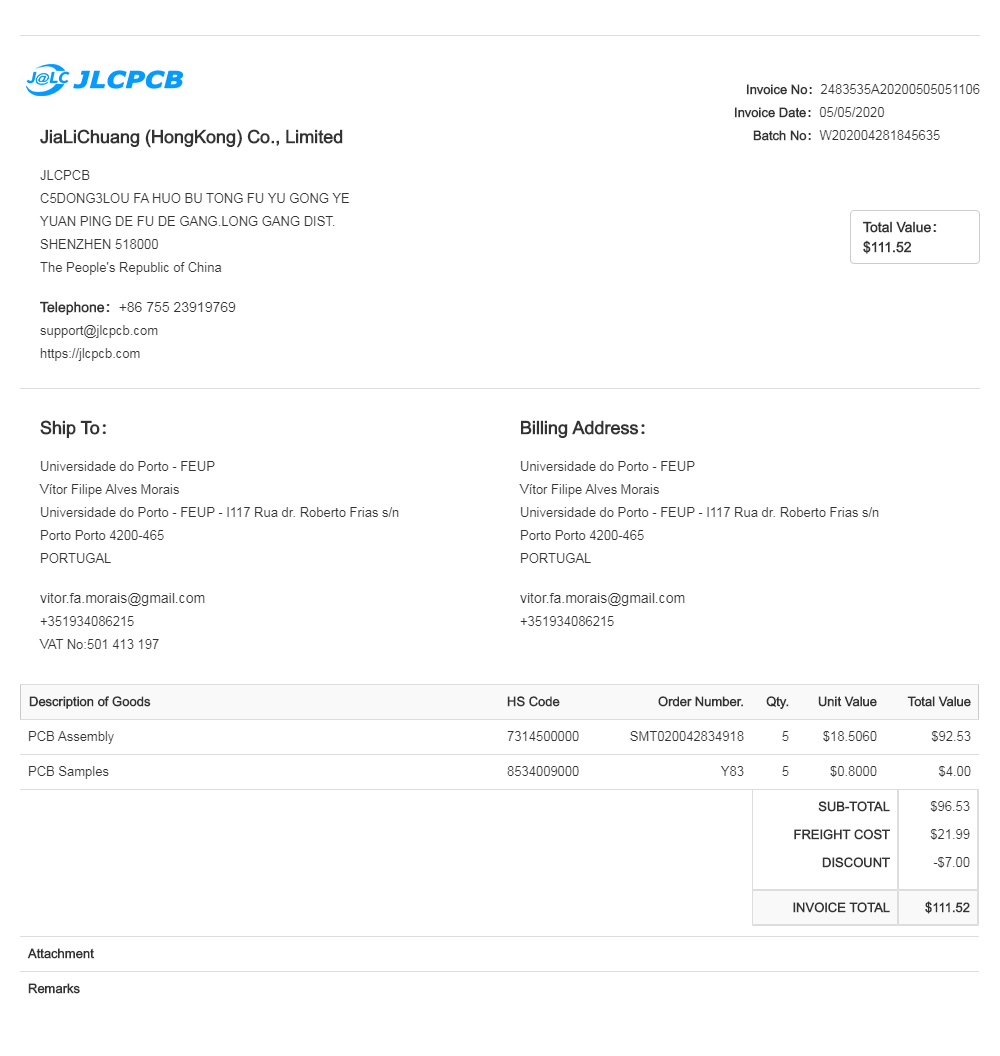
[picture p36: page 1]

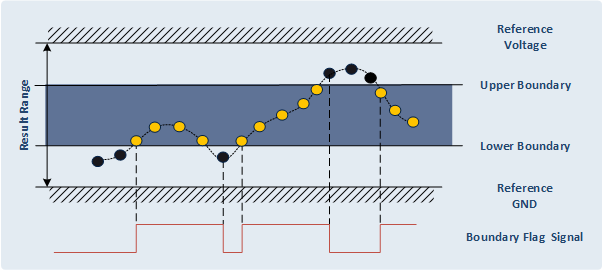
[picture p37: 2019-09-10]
3. Design/1p_inverter_200V_CC/1p_inverter_200V_cc/1p_inverter_200V/Dave/Model/APPS/ADC_MEASUREMENT_ADV/v4_0_14/Uimodel/ADC_measurement_advanced_limitcheck.PNG

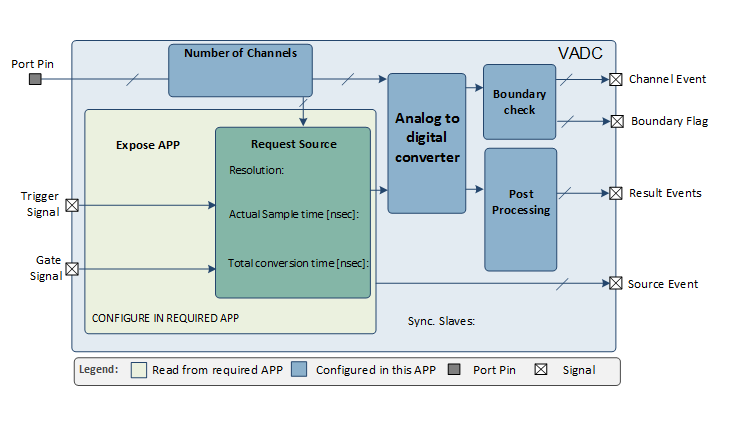
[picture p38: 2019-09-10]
3. Design/1p_inverter_200V_CC/1p_inverter_200V_cc/1p_inverter_200V/Dave/Model/APPS/ADC_MEASUREMENT_ADV/v4_0_14/Uimodel/General_settings_adc_queue_scan.png

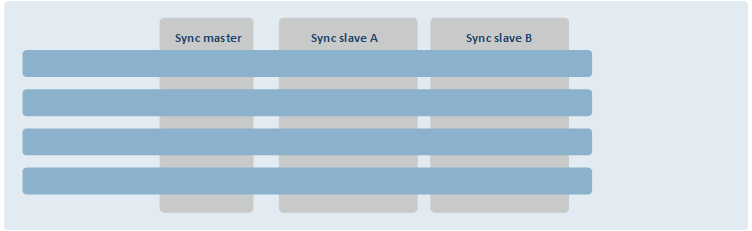
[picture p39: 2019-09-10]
3. Design/1p_inverter_200V_CC/1p_inverter_200V_cc/1p_inverter_200V/Dave/Model/APPS/ADC_MEASUREMENT_ADV/v4_0_14/Uimodel/Sync_2_groups.png

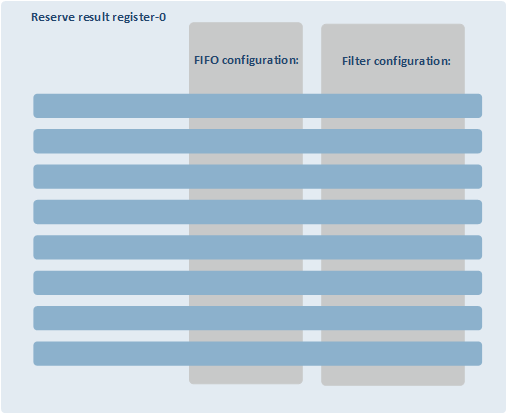
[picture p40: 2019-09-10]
3. Design/1p_inverter_200V_CC/1p_inverter_200V_cc/1p_inverter_200V/Dave/Model/APPS/ADC_MEASUREMENT_ADV/v4_0_14/Uimodel/post_proc_subtraction_mode.png

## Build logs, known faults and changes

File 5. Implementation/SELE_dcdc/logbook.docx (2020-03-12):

# Logbook: project/paper sele_dcdc

The objective of this prohject is to implemente a dc/dc converter, using a three-phase interleaving structure.

This work is a result of academic work of master students framed in electronics course of integrated master in electrical and computers engineering.

This document is aging from end to beginning (the #1 task is the most recent)

# Tasks

1. Proposed software and hardware
  a. 2x converters; one of them in voltage control; the other in current control
2. Hardware setup design
3. Software “get2know”
  a. Load to my ws
  b. Divide into blocks

# Partial results

## Proposed HW and SW

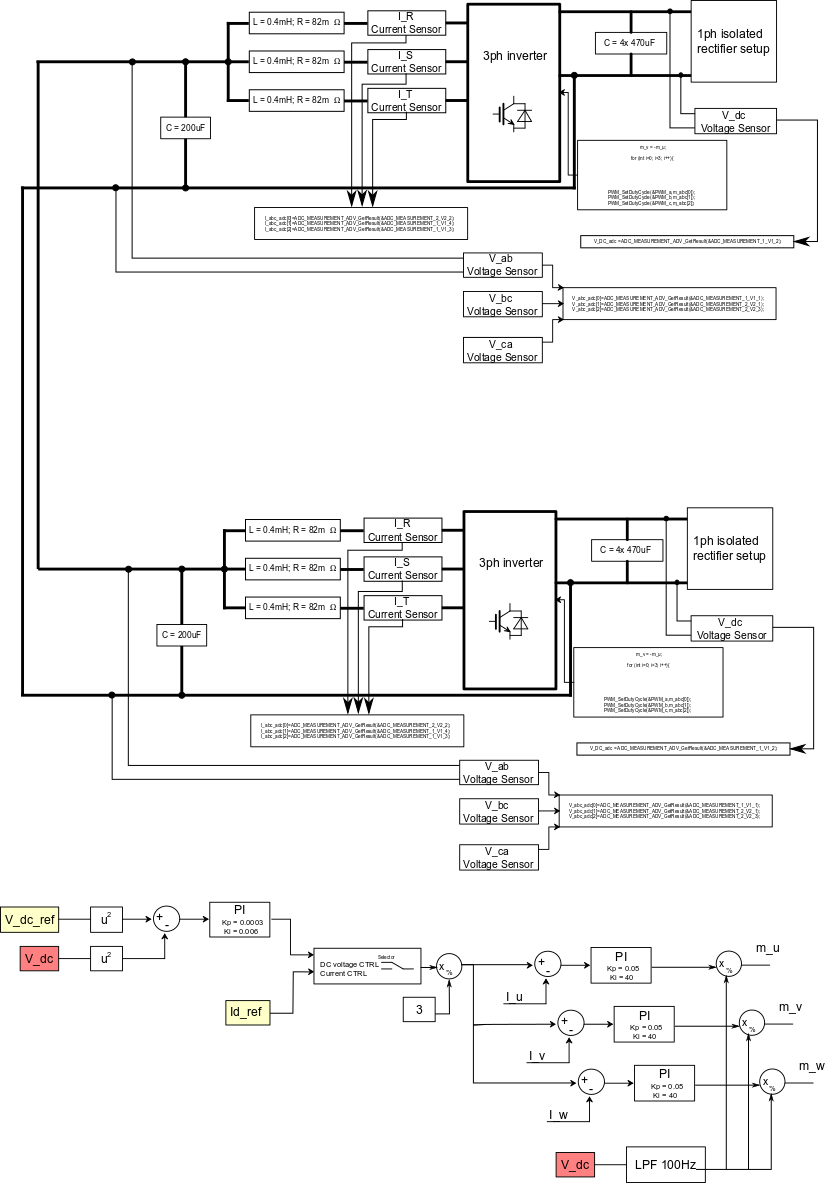
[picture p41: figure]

One of the converters must operate in DC voltage control and the other converter will test the DC voltage loop

## Implemented hardware:

The implemented hardware is presented as following

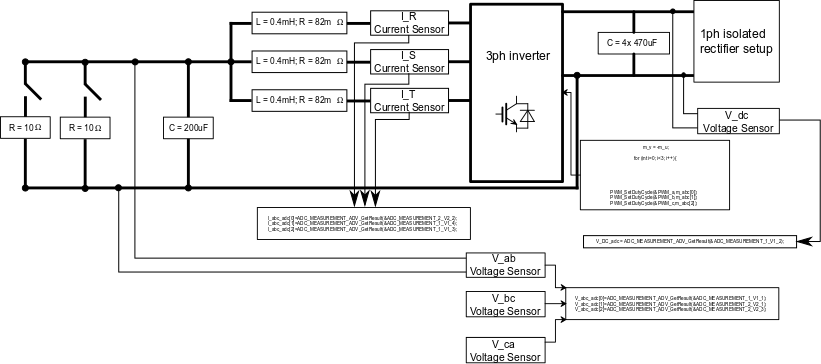
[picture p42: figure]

## Implemented software:

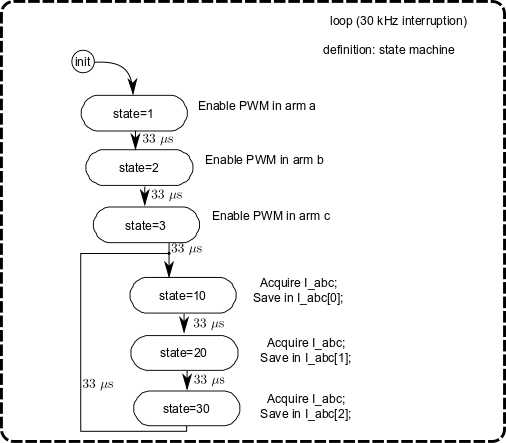
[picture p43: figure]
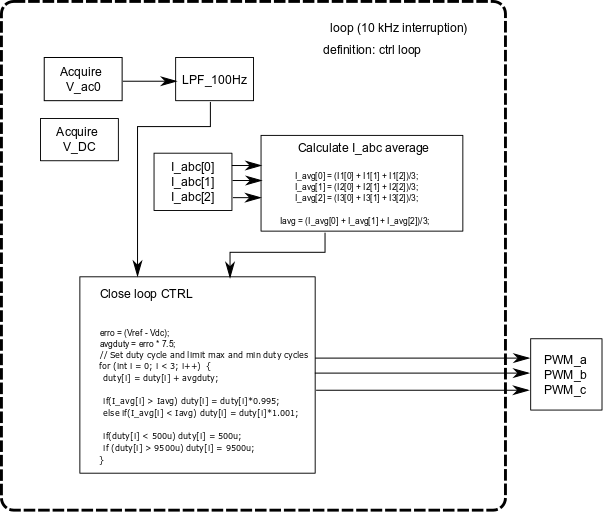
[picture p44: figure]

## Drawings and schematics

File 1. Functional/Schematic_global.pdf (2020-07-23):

# Barramento DC: condensadores e connectores

# Protecção sobrecorrente

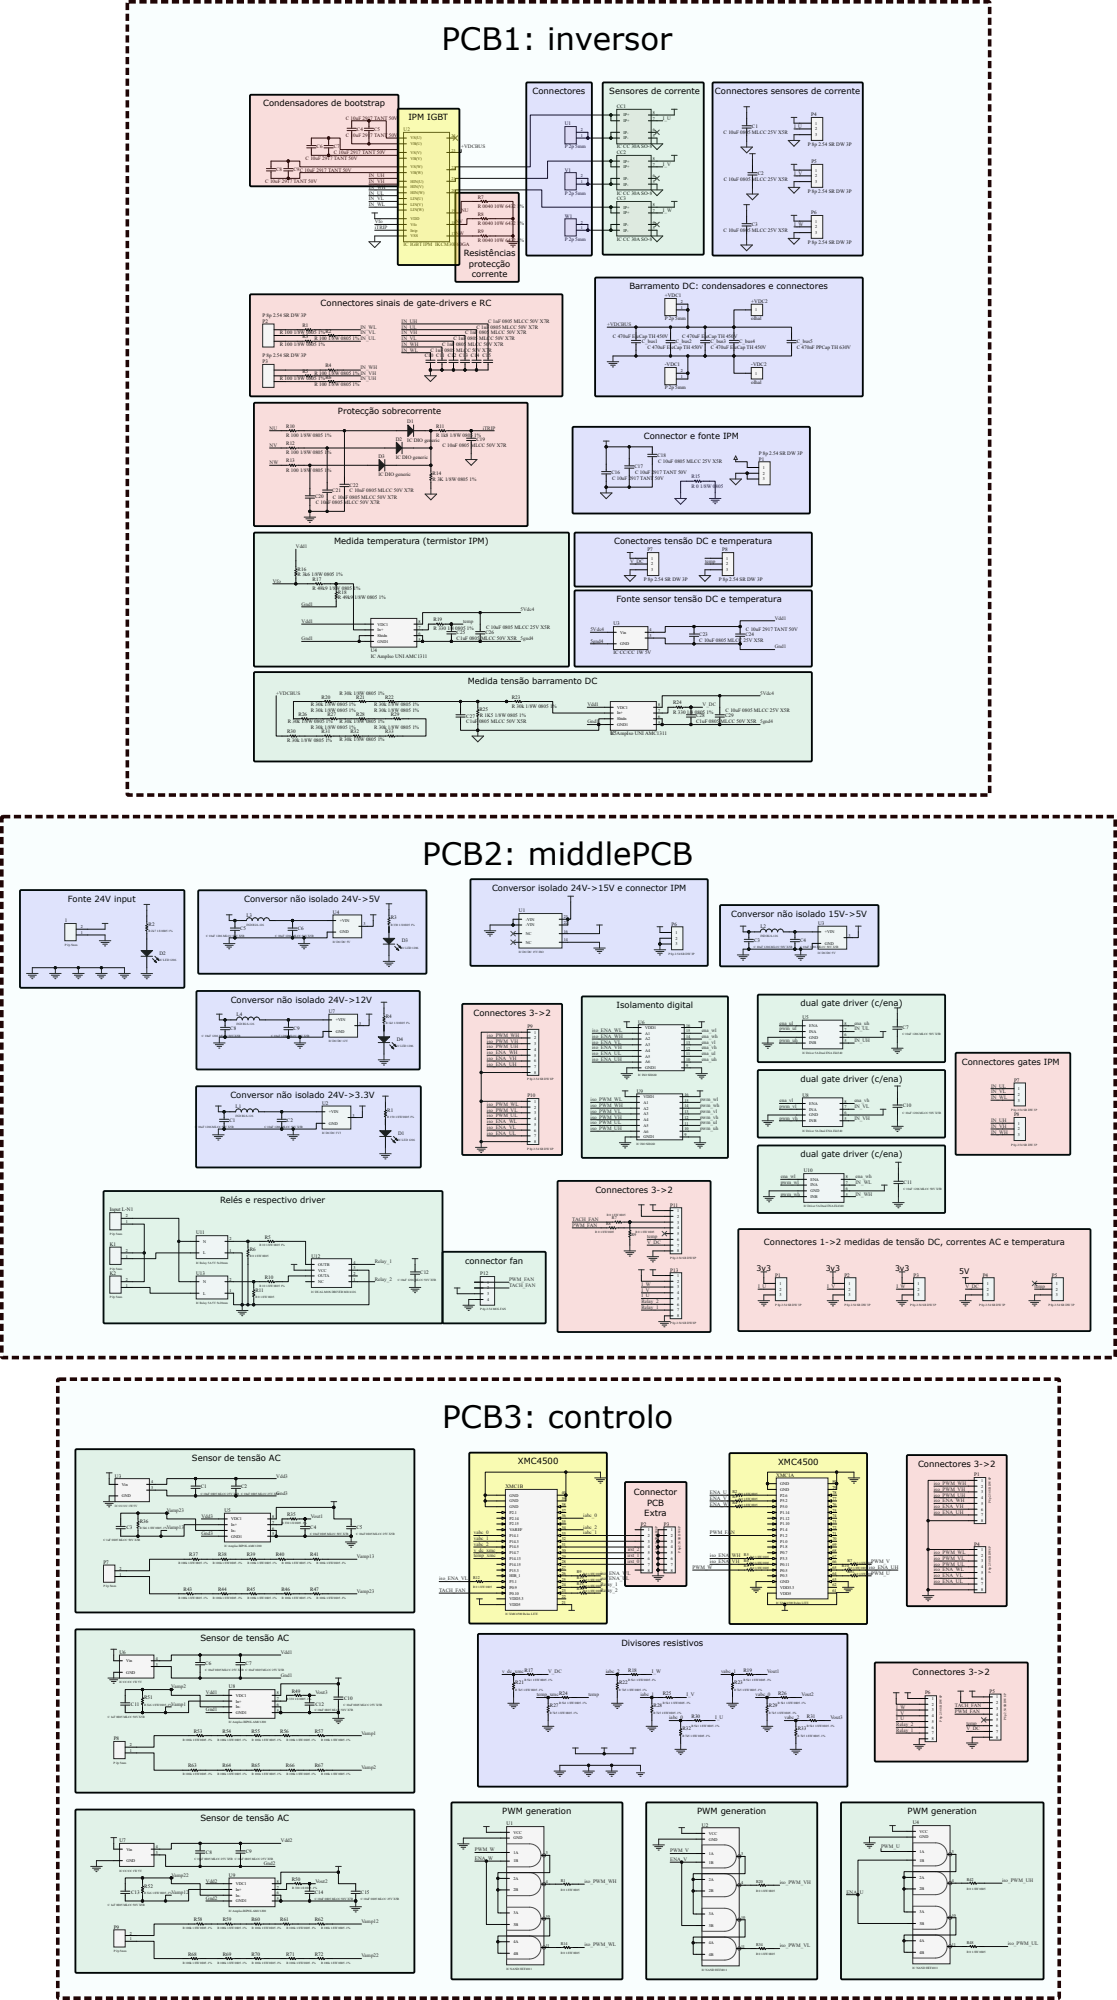
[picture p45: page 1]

Connectores sinais de gate-drivers e RC

Medida temperatura (termistor IPM)

Conectores tensão DC e temperatura

Medida tensão barramento DC

Conversor isolado 24V->15V e connector IPM

IC DC/DC 15V ISO

dual gate driver (c/ena)

IC Driver 5A Dual ENA IX4340

Connectores 1->2 medidas de tensão DC, correntes AC e temperatura

IC DUAL MOS DRIVER MIC4126

Sensor de tensão AC

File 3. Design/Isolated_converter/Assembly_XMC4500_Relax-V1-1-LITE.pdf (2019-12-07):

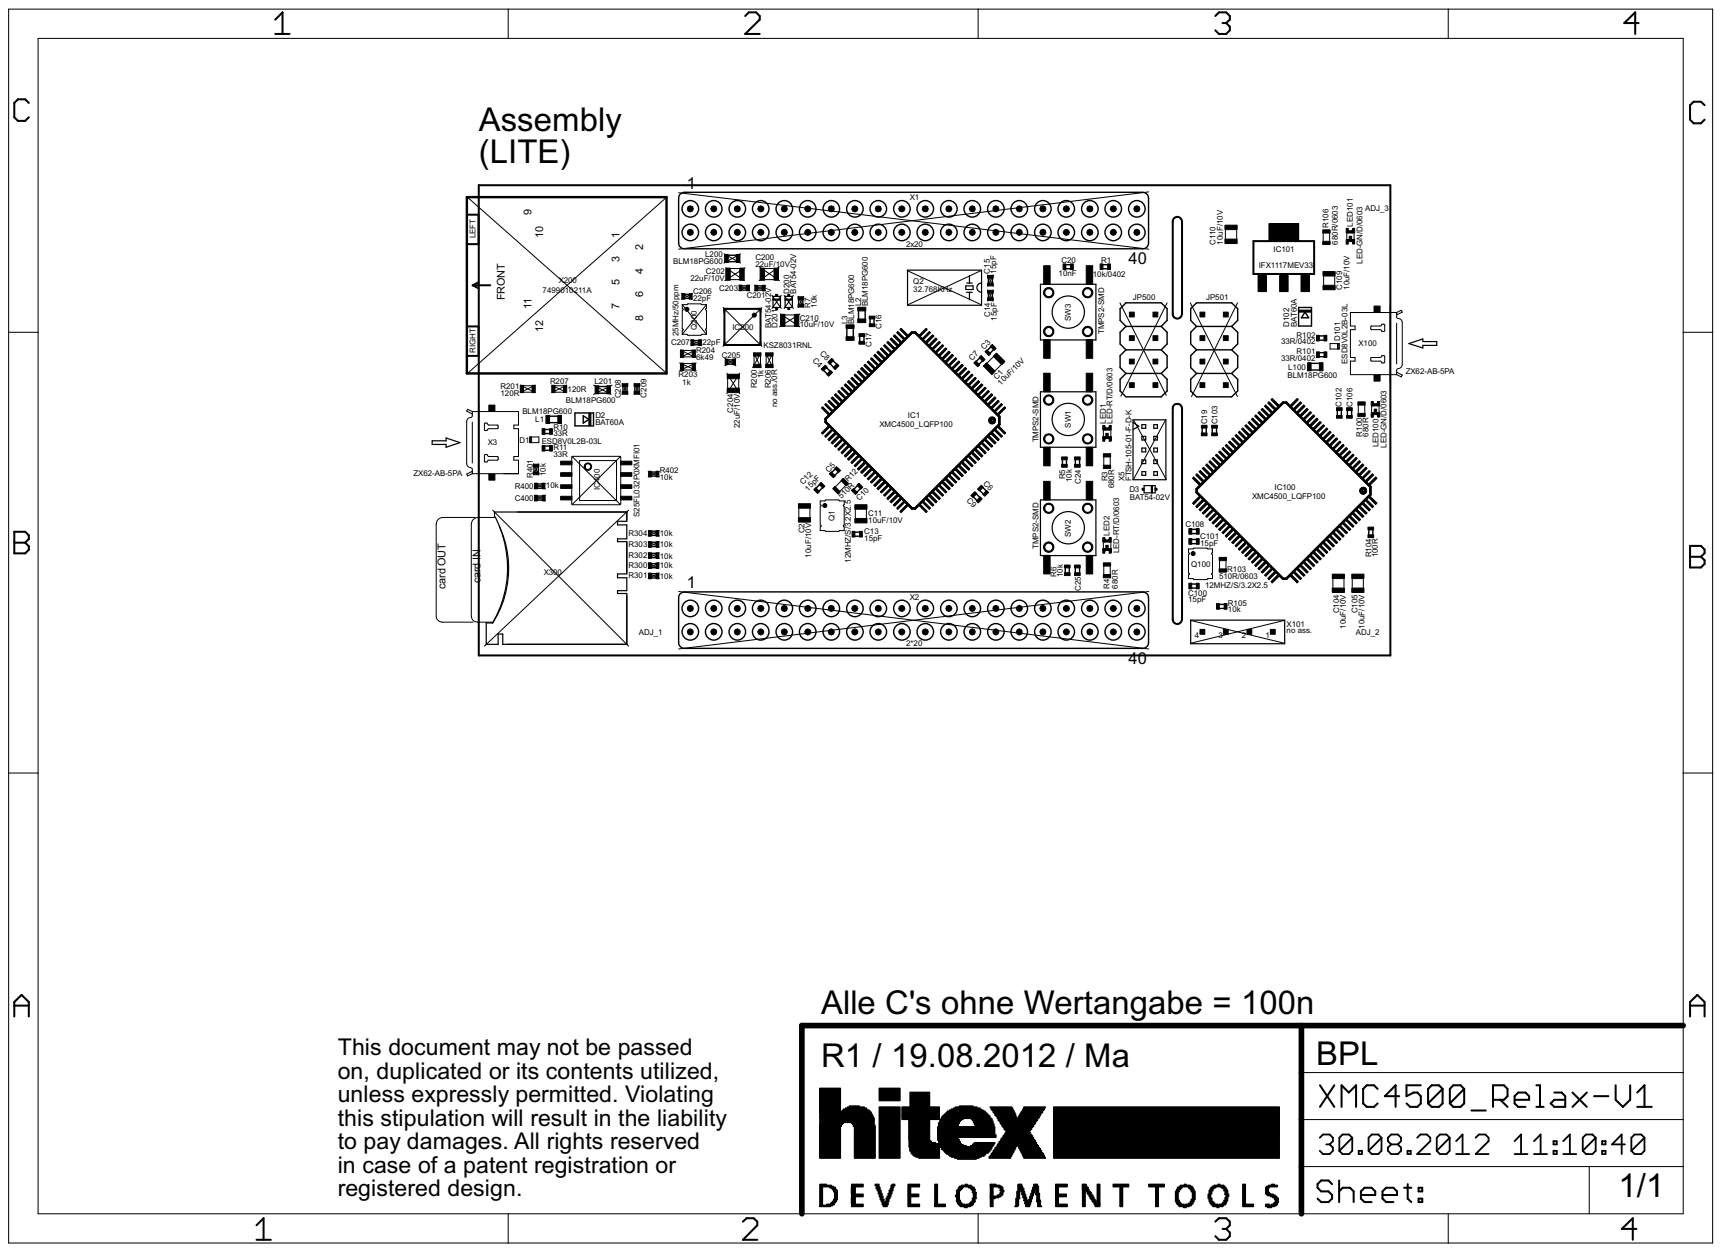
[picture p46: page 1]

This document may not be passed
on, duplicated or its contents utilized, unless expressly permitted. Violating

this stipulation will result in the liability
to pay damages. All rights reserved
in case of a patent registration or
registered design.

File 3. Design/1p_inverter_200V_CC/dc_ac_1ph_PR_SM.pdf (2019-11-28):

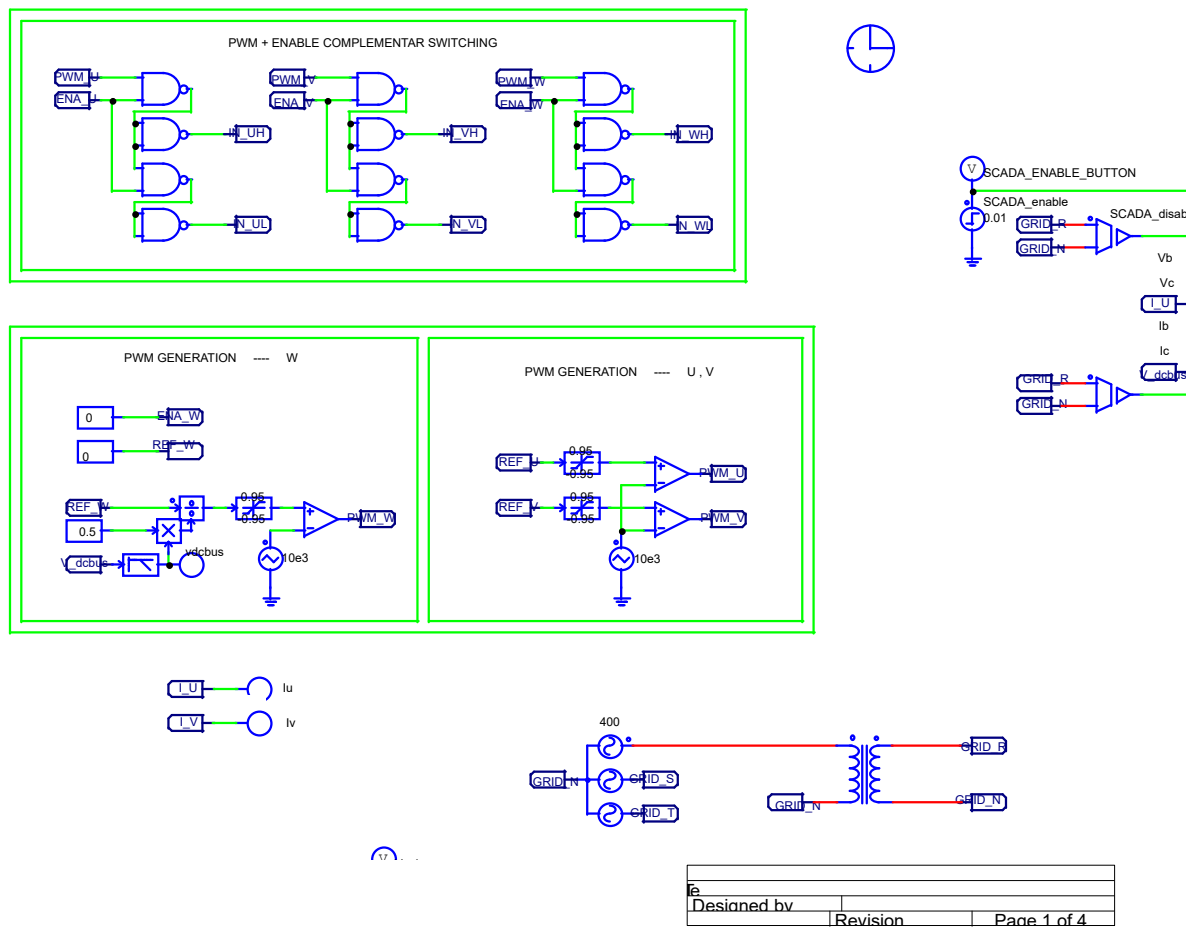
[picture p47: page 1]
Title; Designed by; Revision; Page 1 of 4; PWM_U; ENA_U; PWM_V; ENA_V; PWM_W; ENA_W; PWM GENERATION; REF_W; V_dcbus; vdcbus; GRID_N; GRID_S; GRID_T; V Vu_inv; SCADA_disable 0.01; SCADA_enable; V SCADA_ENABLE_BUTTON; GRID_R; REF_U; REF_V

PWM + ENABLE COMPLEMENTAR SWITCHING

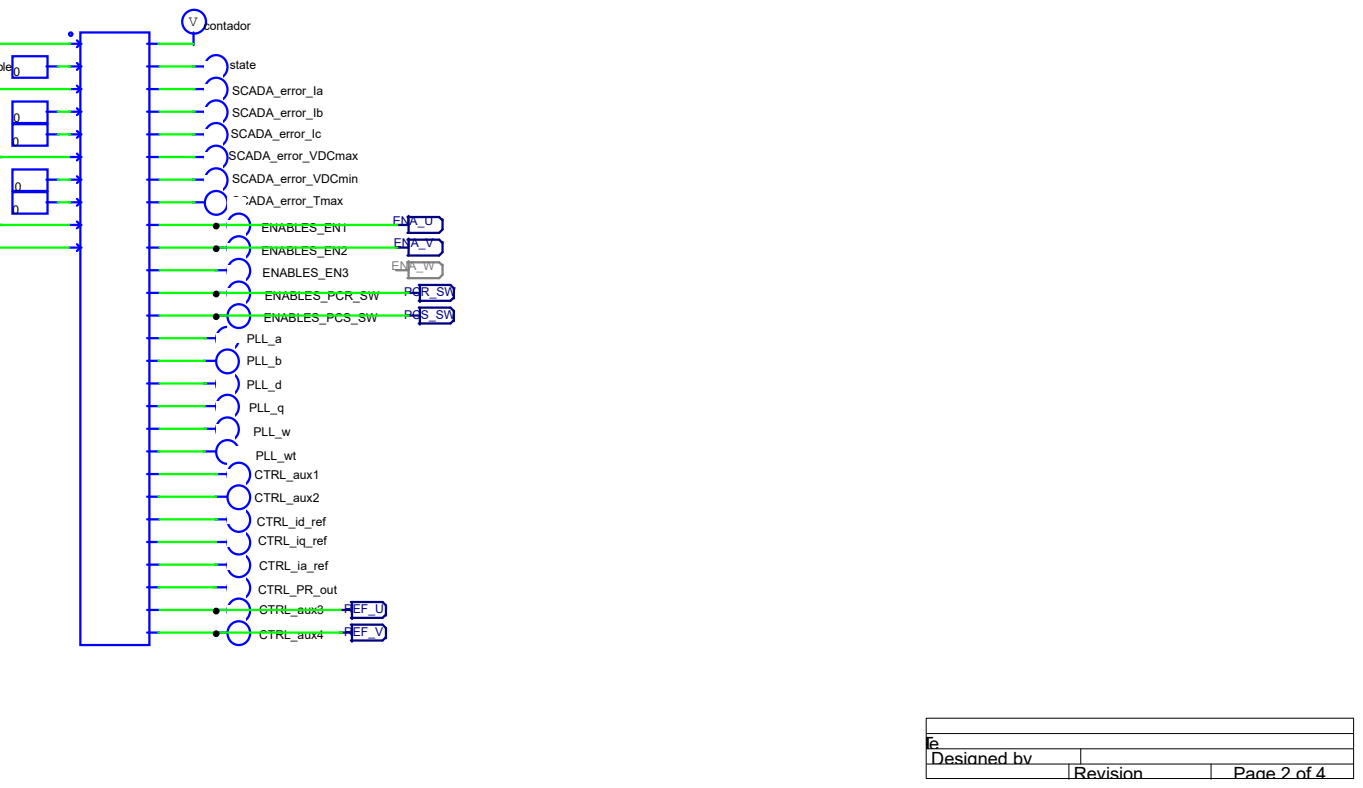
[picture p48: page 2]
V contador; SCADA_disable; state; SCADA_error_Ia; SCADA_error_Ib; SCADA_error_Ic; SCADA_error_VDCmax; SCADA_error_VDCmin; SCADA_error_Tmax; PLL_d; PLL_a; PLL_b; PLL_q; PLL_w; CTRL_PR_out; PLL_wt; CTRL_ia_ref; CTRL_iq_ref; CTRL_id_ref; V_dcbus; CTRL_aux1; ENABLES_EN1; ENABLES_EN2; ENABLES_EN3; ENABLES_PCR_SW; ENABLES_PCS_SW; CTRL_aux2; CTRL_aux3; CTRL_aux4; PCR_SW; PCS_SW; ENA_U; ENA_V; ENA_W; REF_U; REF_V

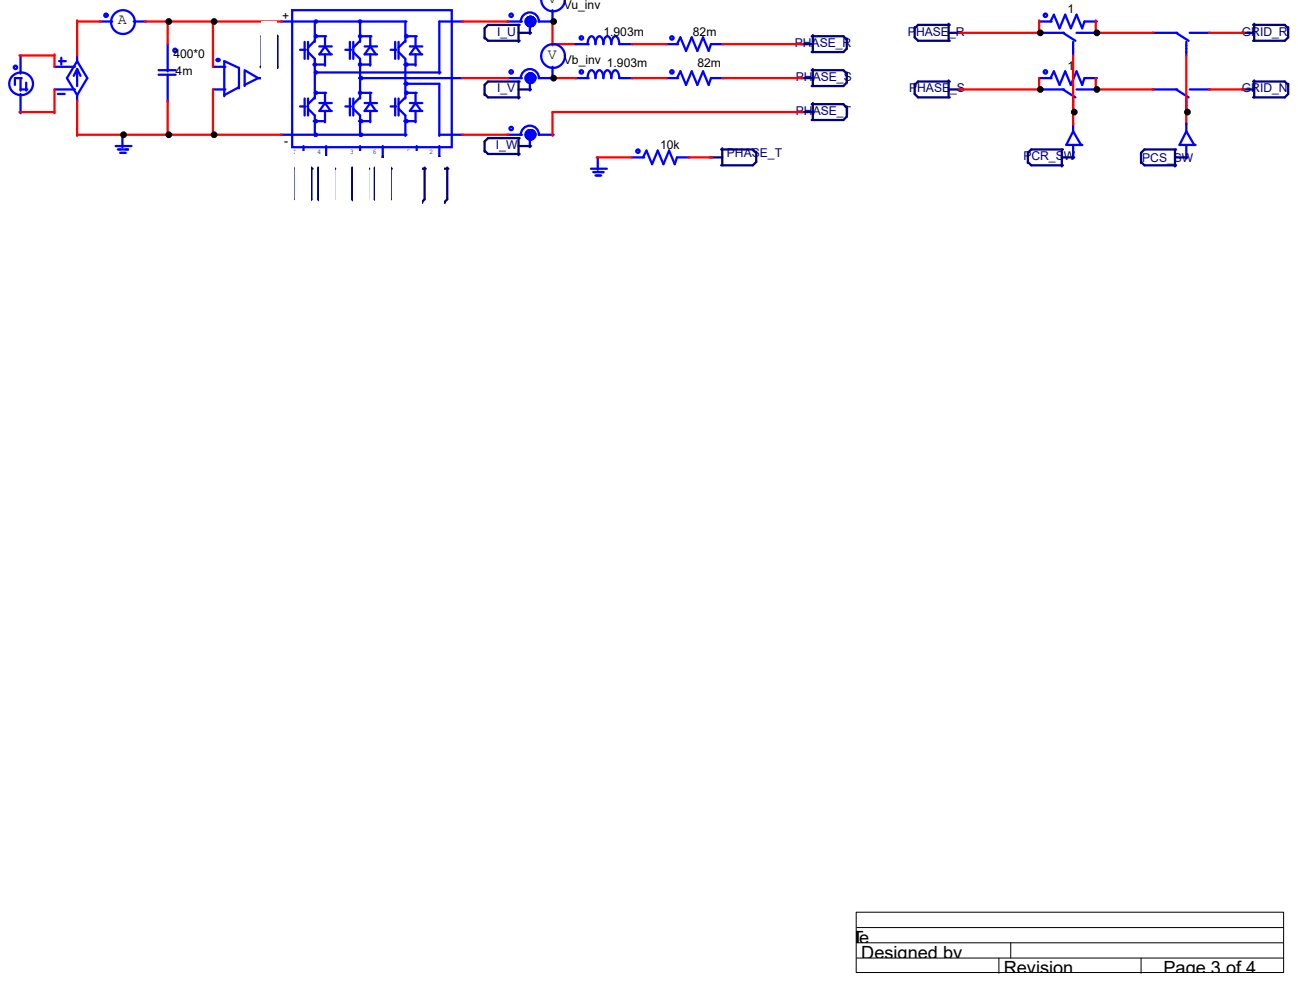
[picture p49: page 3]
PHASE_R; PHASE_S; PHASE_T; GRID_R; GRID_N; V Vu_inv; V Vb_inv; PCR_SW; PCS_SW

Designed by | Vítor Morais rev 1.0

FEUP

1

Title | single_phase_converter

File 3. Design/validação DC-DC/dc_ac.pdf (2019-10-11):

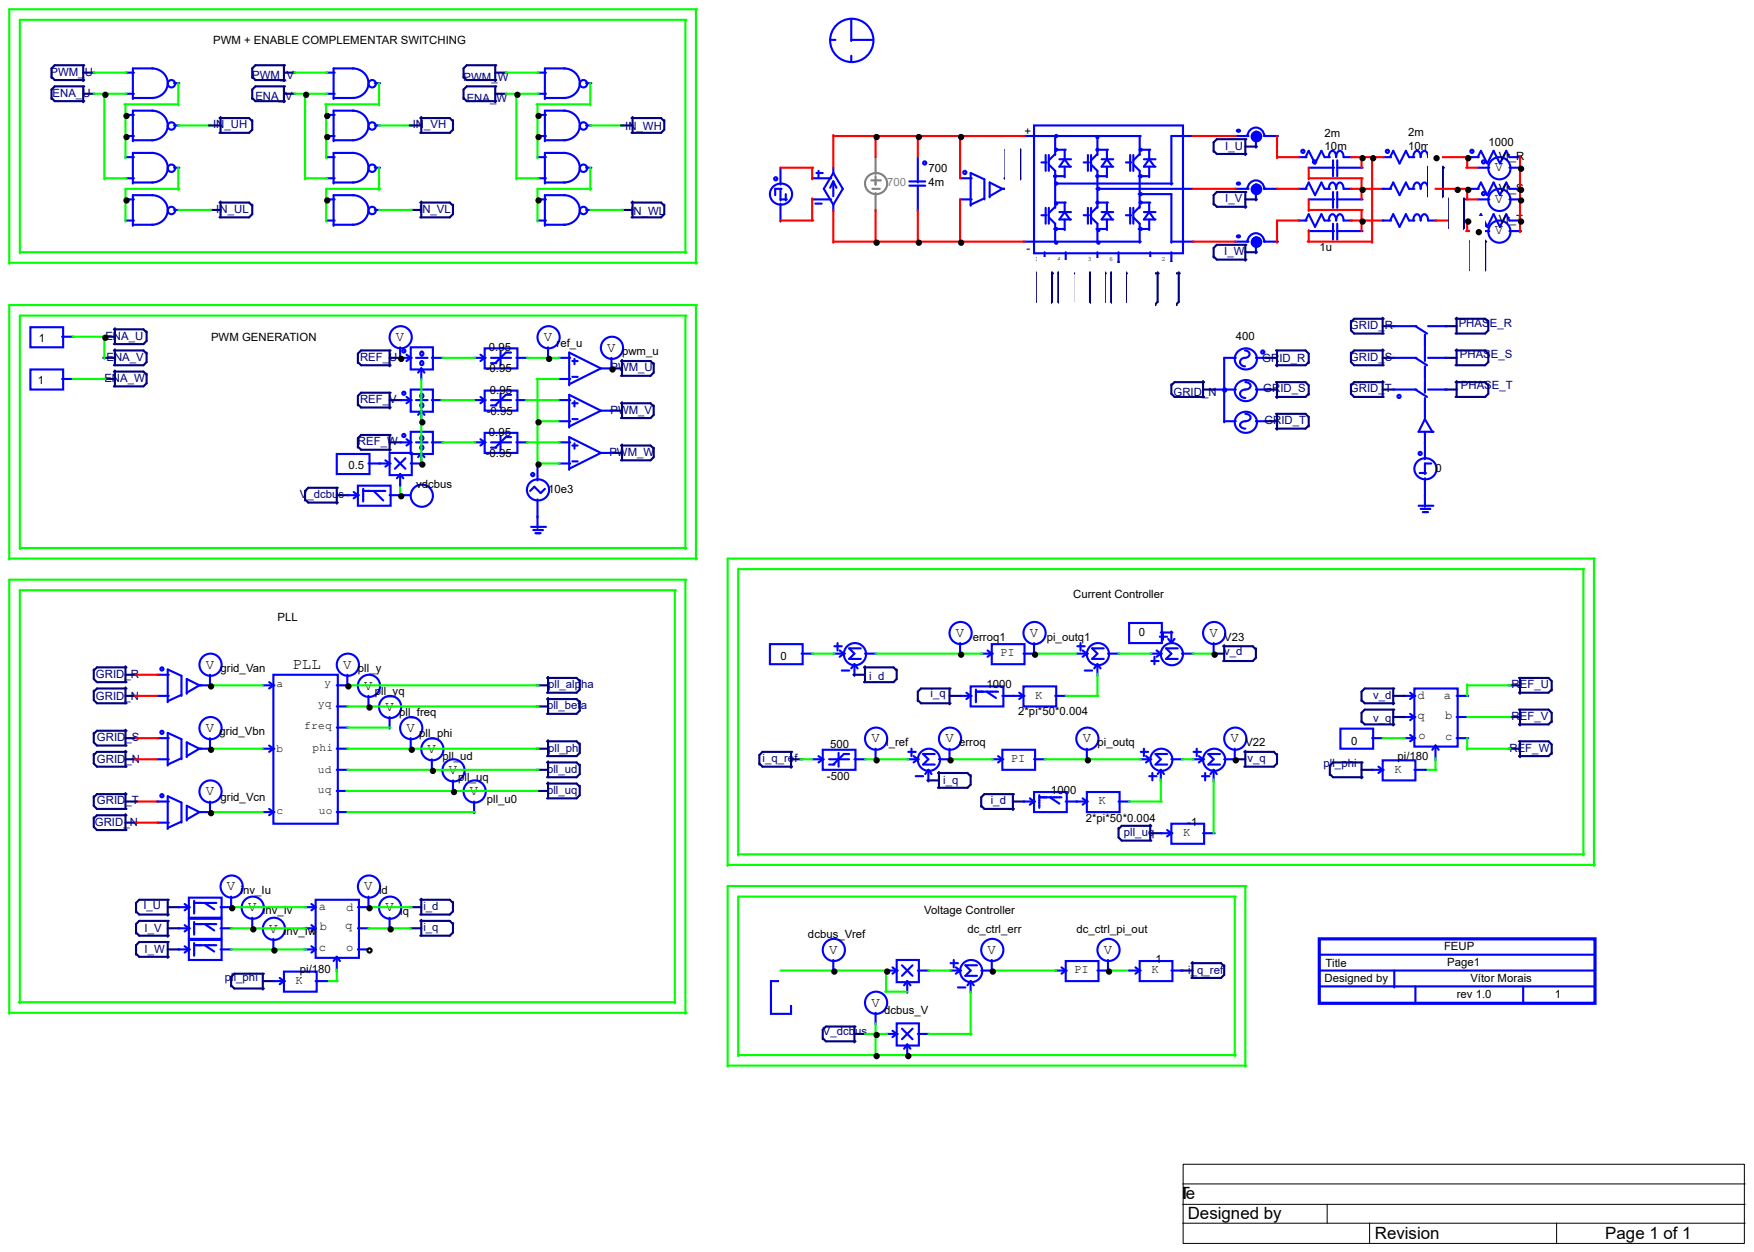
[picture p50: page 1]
Title Designed by; Revision; Page 1 of 1; PWM_U; ENA_U; PWM_V; ENA_V; PWM_W; ENA_W; PWM GENERATION; REF_U; REF_V; REF_W; V pwm_u; V ref_u; V_dcbus; vdcbus; PLL; freq; phi; V pll_y; V pll_yq; V pll_freq; V pll_phi; V pll_ud; Vpll_uq; V pll_u0; pll_alpha; pll_beta; pll_phi; V inv_Iu; pll_ud; pll_uq; PHASE_R; PHASE_S; PHASE_T; GRID_R; GRID_S; GRID_T; V grid_Van; V erroq; V pi_outq; V erroq1; V pi_outq1; V i_ref; i_q_ref; GRID_N; V grid_Vbn; V grid_Vcn; V inv_Iv; V inv_Iw; Current Controller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

PWM + ENABLE COMPLEMENTAR SWITCHING

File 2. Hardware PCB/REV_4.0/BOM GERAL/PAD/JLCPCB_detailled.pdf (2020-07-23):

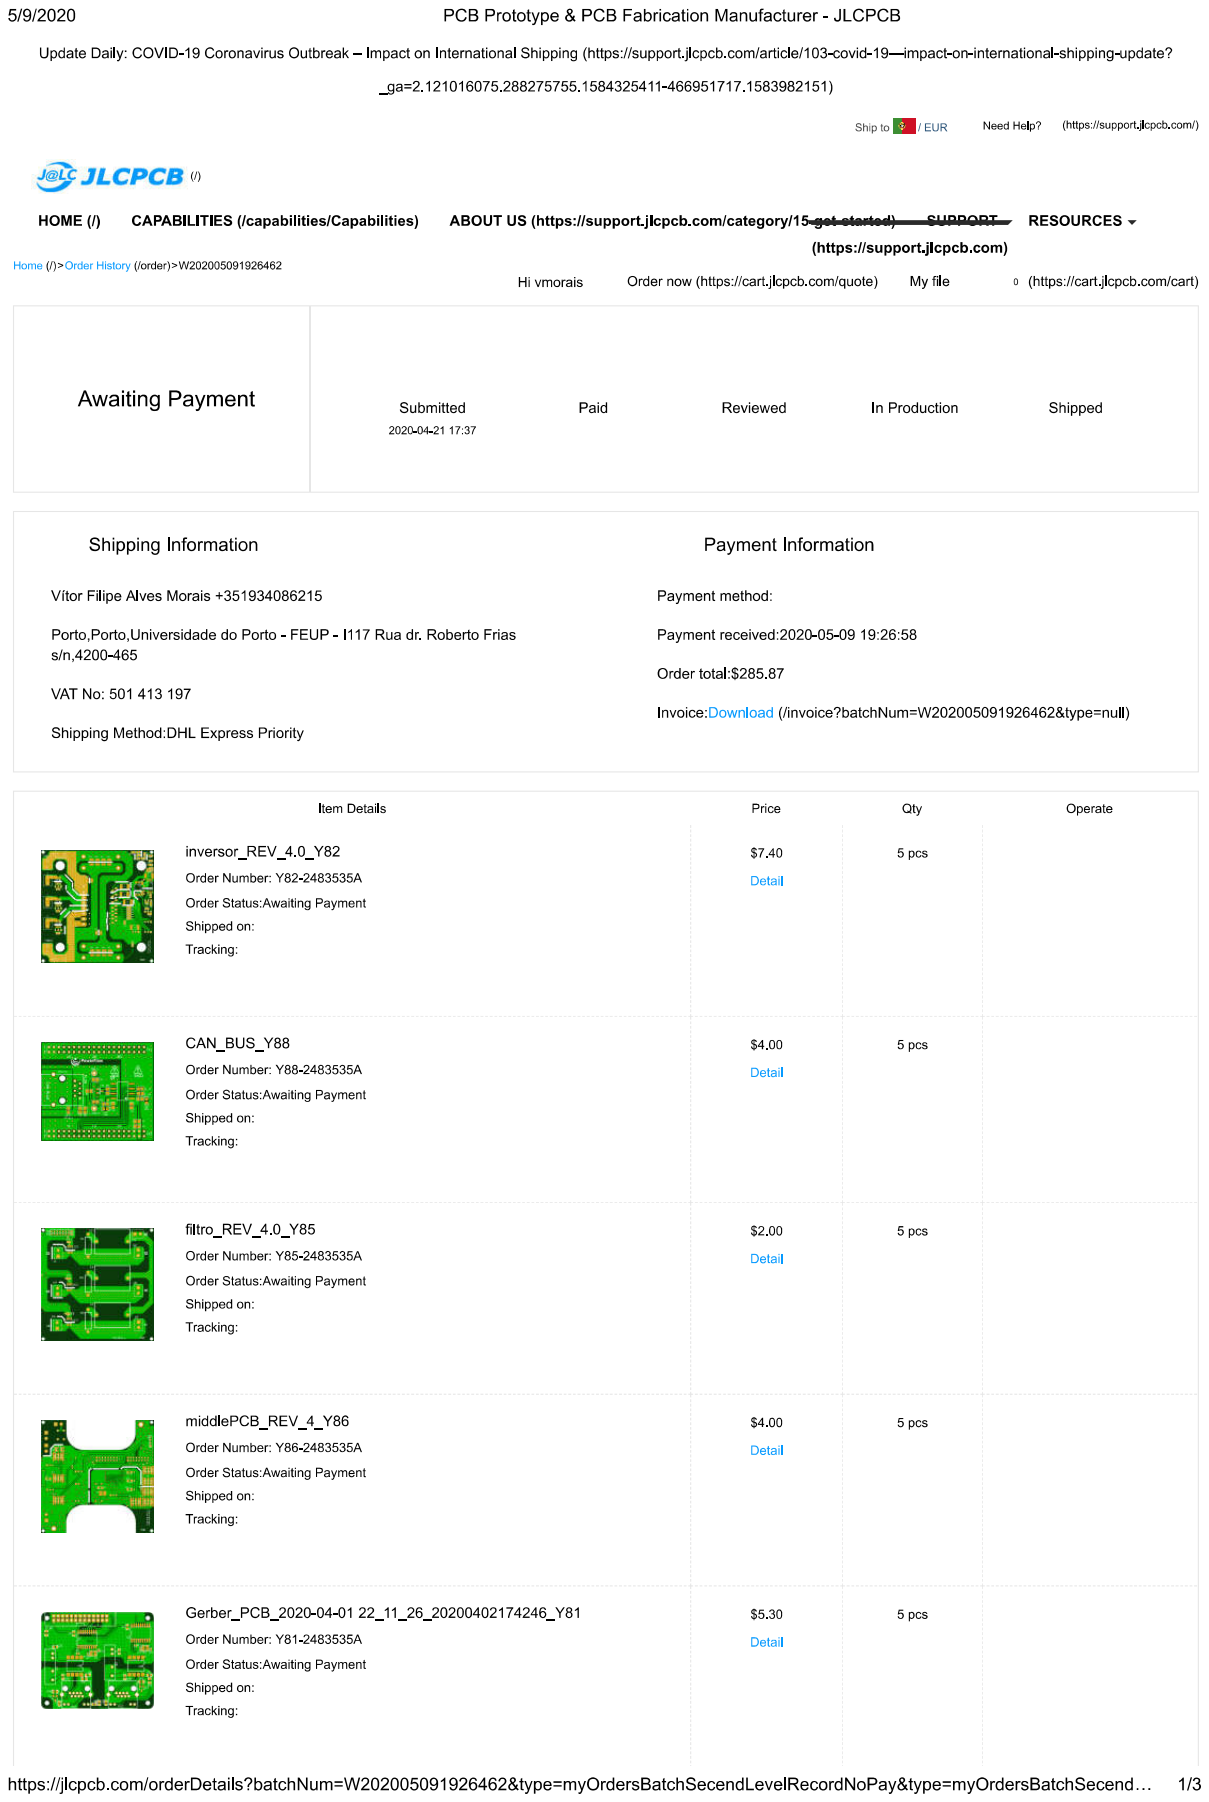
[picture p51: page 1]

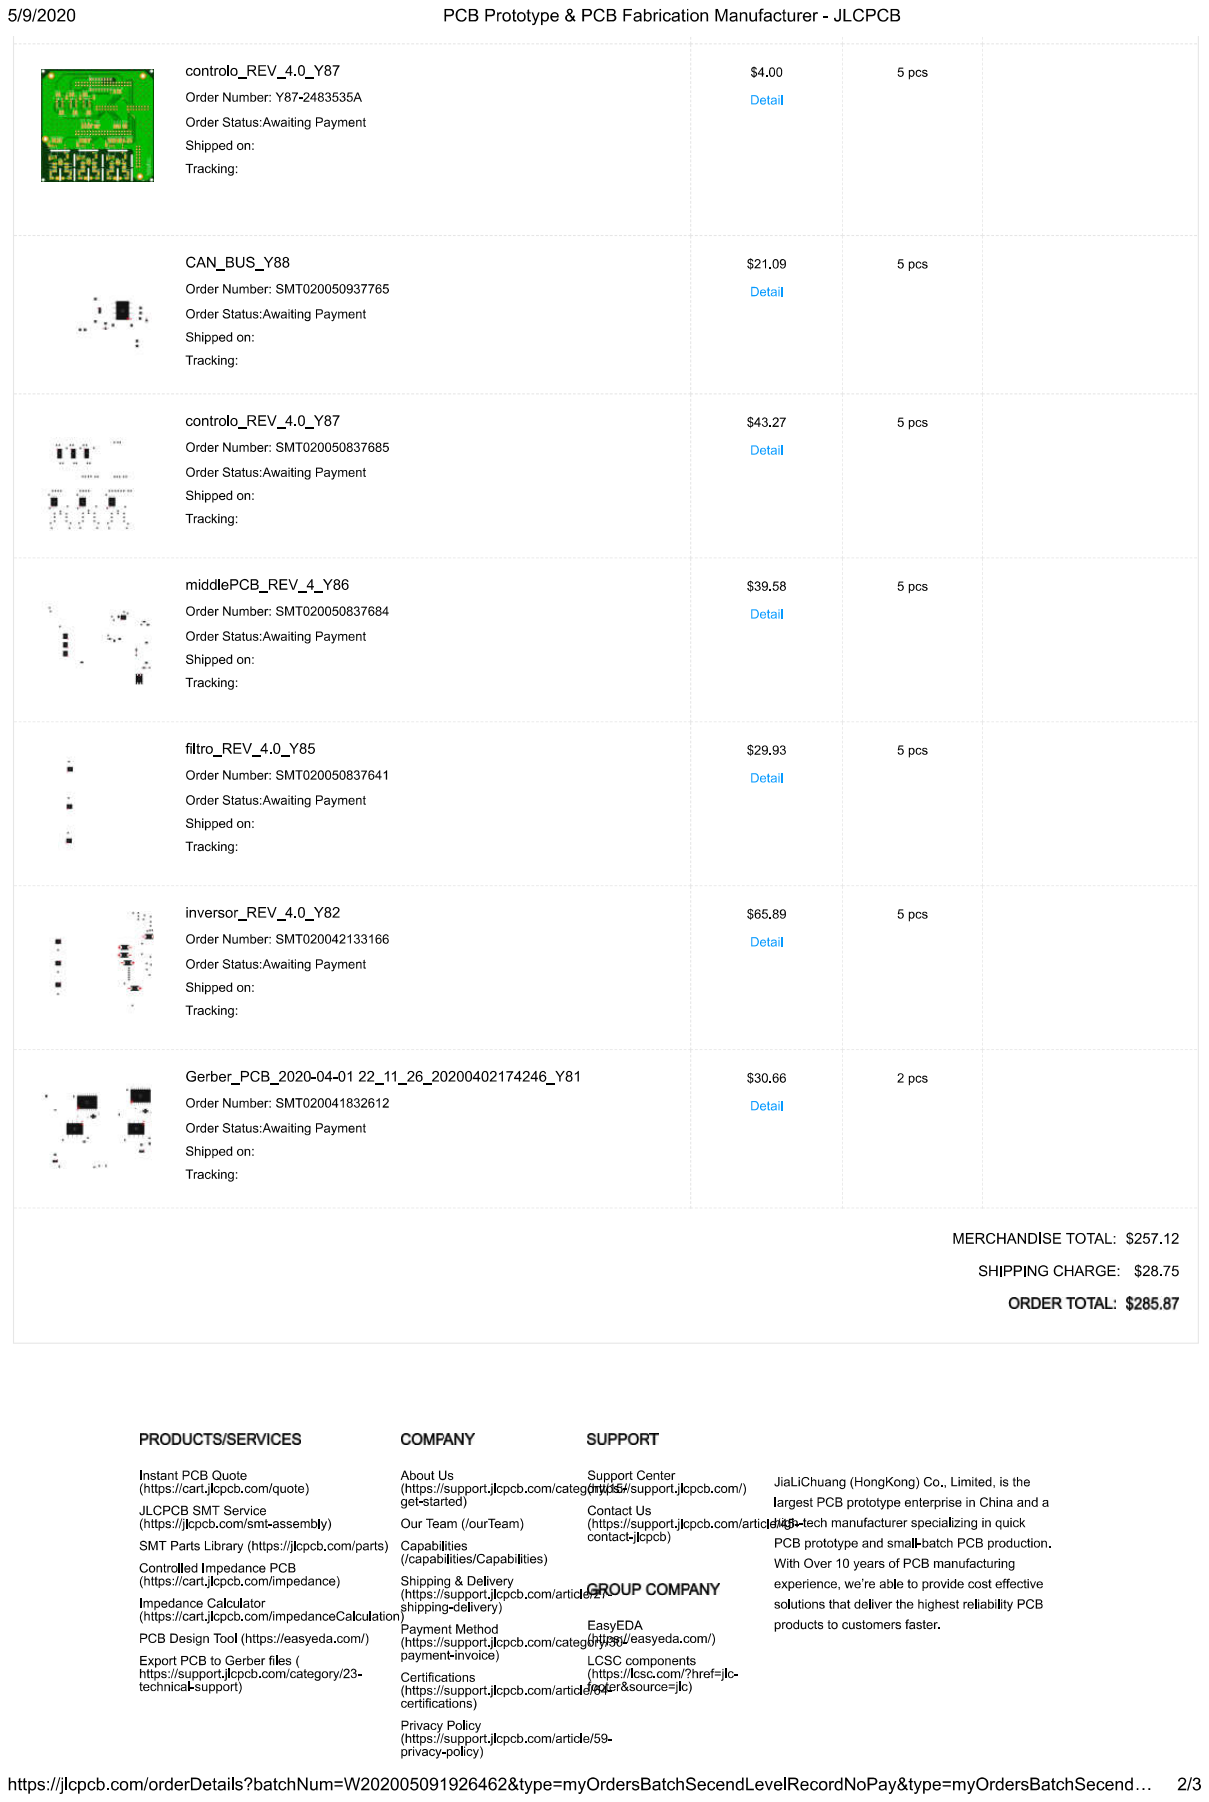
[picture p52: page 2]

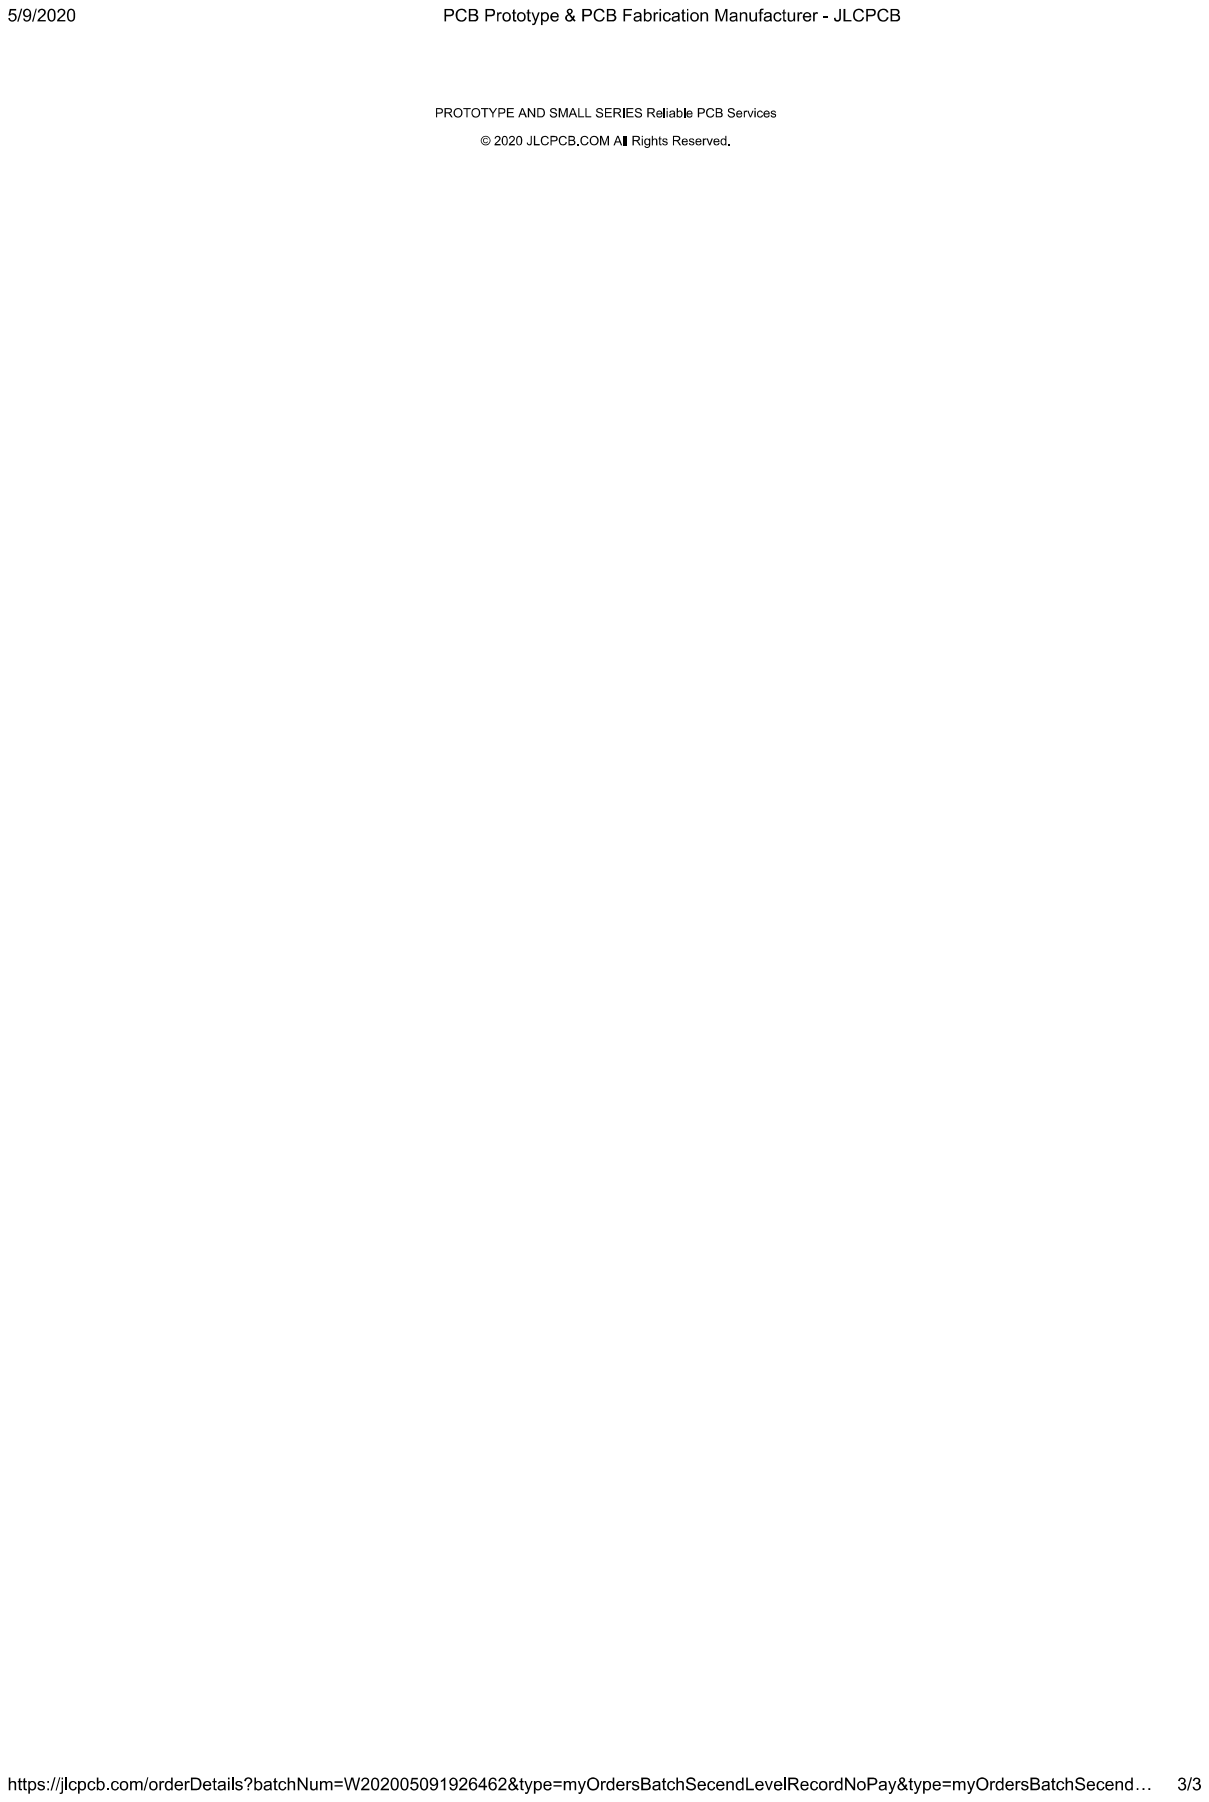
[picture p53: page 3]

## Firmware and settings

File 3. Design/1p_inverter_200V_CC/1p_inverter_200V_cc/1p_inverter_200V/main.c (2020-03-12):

/*
 * main.c
 *
 *  Created on: 2019 Nov 21 12
 *  Author: VMORAIS
 *	Version 1p_inv
 */

#include <DAVE.h>                 //Declarations from DAVE Code Generation (includes SFR declaration)
#include <probe_scope.h>
#include "init.h"
#include "functions.h"
#include "CTRL_functions.h"

float scope1, scope2, scope3;
uint32_t scopeu1, scopeu2, scopeu3;
uint32_t counter=1u;
uint32_t fault=0u;

float vDQp_ref[2]={1.0f, 0.0f};
float vDQp[2]={0.0f, 0.0f};
float vABp[2]={0.0f, 0.0f};

float vDQn_ref[2]={0.0f, 0.0f};
float vDQn[2]={0.0f, 0.0f};
float vABn[2]={0.0f, 0.0f};
float Vn=0.5f, V5=0.0f, V7=0.0f, V11=0.0f, V13=0.0f;

float vDQ5[2]={0.0f, 0.0f};
float vAB5[2]={0.0f, 0.0f};
float vabc5[3]={0.0f, 0.0f, 0.0f};
float vDQ7[2]={0.0f, 0.0f};
float vAB7[2]={0.0f, 0.0f};
float vabc7[3]={0.0f, 0.0f, 0.0f};
float vDQ11[2]={0.0f, 0.0f};
float vAB11[2]={0.0f, 0.0f};
float vabc11[3]={0.0f, 0.0f, 0.0f};
float vDQ13[2]={0.0f, 0.0f};
float vAB13[2]={0.0f, 0.0f};
float vabc13[3]={0.0f, 0.0f, 0.0f};

float vmAB[2]={0.0f, 0.0f};

float vmabc[3]={0.0f, 0.0f, 0.0f};

float wt_buff5=0.0f, wt_buff7=0.0f, wt_buff11=0.0f, wt_buff13=0.0f;
float wt5=0.0f, wt7=0.0f, wt11=0.0f, wt13=0.0f;
float wt_jump=0.0f;

////  vĂ­tor
float scope_adc1, scope_adc2, scope_adc3, scope_adc4, scope_adc5, scope_adc6, scope_adc7;
float aux_var1, aux_var2, aux_var3, aux_var4, aux_var5, aux_var6, aux_var7;

float LPFbuff_vdc[2] = {0.0f, 0.0f};
float LPFbuff_temp[2] = {0.0f, 0.0f};
float LPFbuff_v[2] = {0.0f, 0.0f};
float LPFbuff_v2[2] = {0.0f, 0.0f};

float AB_aux[2] = {0.0f, 0.0f};
float dq_aux[2] = {0.0f, 0.0f};
float wt_aux = 0.0f;
float w_aux = 100.0f*PI;
float LPFbuff_w_aux[2] = {0.0f, 0.0f};
float LPFbuff_dq1_aux[2] = {0.0f, 0.0f};
float LPFbuff_dq2_aux[2] = {0.0f, 0.0f};

//// filters ADC AC
float ADC_LPFbuff_VA[2] = {0.0f, 0.0f}; 
float ADC_LPFbuff_VB[2] = {0.0f, 0.0f}; 
float ADC_LPFbuff_VC[2] = {0.0f, 0.0f}; 
float ADC_LPFbuff_IA[2] = {0.0f, 0.0f}; 
float ADC_LPFbuff_IB[2] = {0.0f, 0.0f}; 
float ADC_LPFbuff_IC[2] = {0.0f, 0.0f}; 


int SCADA_enable = 0;			//ON-OFF micrium button
int SCADA_disable = 0;			//ON-OFF micrium button
int SCADA_status_button = 0;    //ON-OFF micrium button
float SCADA_Imax = 15.0f;		//Maximum current
float SCADA_VDCmax = 180.0f;	//Maximum Voltage DCBUS
float SCADA_VDCmin = -10.0f;	//Minimum Voltage DCBUS
float SCADA_Tmax = 60.0f;		//Maximum converter temperature

int SCADA_error_Ia = 0;			//Flag
int SCADA_error_Ib = 0;			//Flag
int SCADA_error_Ic = 0;			//Flag
int SCADA_error_VDCmax = 0;		//Flag
int SCADA_error_VDCmin = 0;		//Flag
int SCADA_error_Tmax = 0;		//Flag
int timer_sm = 0;

float SCADA_Id_ref = 0;
float SCADA_Iq_ref = 0;
float SCADA_Vdc_ref = 200;


uint8_t no_fault(void) {
	if ( (I_abc[0] > SCADA_Imax) || (I_abc[0] < -SCADA_Imax) ||
			(I_abc[1] > SCADA_Imax) || (I_abc[1] < -SCADA_Imax) ||
			(I_abc[2] > SCADA_Imax) || (I_abc[2] < -SCADA_Imax) ||
			(conv.Vdc > SCADA_VDCmax) ||
			(conv.Vdc < SCADA_VDCmin) ||
			(conv.temp > SCADA_Tmax)) {
		return 1;
	}
	else {
		return 0;
	}

}

void ConverterStateMachine(void){

	timer_sm += 1;
	switch(state){
	case init:
		if ((SCADA_enable==1) && (timer_sm > (500*_1MS))) {
			state = pc1;
			timer_sm = 0;
		}
		break;
	case pc1:
		if ((timer_sm > (500*_1MS)) && (conv.Vdc > 120.0f)/**/) {
			state = pc2;
			timer_sm = 0;
		}
		if (SCADA_disable==1) {
			//SCADA_enable = 0;
			state = init;
			timer_sm = 0;
		}
		break;
	case pc2:
		if (timer_sm > (500*_1MS) ){
			state = idle;
			timer_sm = 0;
		}
		if (SCADA_disable==1) {
			//SCADA_enable = 0;
			state = init;
			timer_sm = 0;
		}
		break;
	case idle:
		if (SCADA_enable==1 && no_fault()==0 ) {
			//SCADA_enable = 0;
			SCADA_error_Ia = 0;
			SCADA_error_Ib = 0;
			SCADA_error_Ic = 0;
			SCADA_error_VDCmax = 0;
			SCADA_error_VDCmin = 0;
			SCADA_error_Tmax = 0;
			state = running;
		}
		if (SCADA_disable==1) {
			//SCADA_enable = 0;
			state = init;
			timer_sm = 0;
		}
		break;
	case running:
		if (SCADA_disable==1) {
			//SCADA_enable = 0;
			state = init;
		}
		//FALHAS
		if ((I_abc[0] > SCADA_Imax) || (I_abc[0] < -SCADA_Imax)) {
			state = init;
			SCADA_error_Ia = 1;
		}
		if ((I_abc[1] > SCADA_Imax) || (I_abc[1] < -SCADA_Imax)) {
			state = init;
			SCADA_error_Ib = 1;
		}
		if ((I_abc[2] > SCADA_Imax) || (I_abc[2] < -SCADA_Imax)) {
			state = init;
			SCADA_error_Ic = 1;
		}
		if ((conv.Vdc > SCADA_VDCmax)) {
			state = init;
			SCADA_error_VDCmax = 1;
		}
		if ((conv.Vdc < SCADA_VDCmin)) {
			state = init;
			SCADA_error_VDCmin = 1;
		}
		if ((conv.temp > SCADA_Tmax)) {
			state = init;
			SCADA_error_Tmax = 1;
		}
		break;
	}


	if (state==init){
		DIGITAL_IO_SetOutputLow(&EN_1);
		DIGITAL_IO_SetOutputLow(&EN_2);
		DIGITAL_IO_SetOutputLow(&EN_3);
		DIGITAL_IO_SetOutputLow(&SSR1);//PCR_SW = 0;
		DIGITAL_IO_SetOutputLow(&SSR2);//PCS_SW = 0;
		SCADA_status_button = 0;
	}
	else if (state==pc1){
		DIGITAL_IO_SetOutputLow(&EN_1);
		DIGITAL_IO_SetOutputLow(&EN_2);
		DIGITAL_IO_SetOutputLow(&EN_3);
		DIGITAL_IO_SetOutputLow(&SSR1);//PCR_SW = 0;
		DIGITAL_IO_SetOutputHigh(&SSR2);//PCS_SW = 1;
		SCADA_status_button = 0;
	}
	else if (state==pc2){
		DIGITAL_IO_SetOutputLow(&EN_1);
		DIGITAL_IO_SetOutputLow(&EN_2);
		DIGITAL_IO_SetOutputLow(&EN_3);
		DIGITAL_IO_SetOutputHigh(&SSR1);//PCR_SW = 1;
		DIGITAL_IO_SetOutputHigh(&SSR2);//PCS_SW = 1;
		SCADA_status_button = 0;
	}
	else if (state==idle){
		DIGITAL_IO_SetOutputLow(&EN_1);
		DIGITAL_IO_SetOutputLow(&EN_2);
		DIGITAL_IO_SetOutputLow(&EN_3);
		DIGITAL_IO_SetOutputHigh(&SSR1);//PCR_SW = 1;
		DIGITAL_IO_SetOutputHigh(&SSR2);//PCS_SW = 1;
		SCADA_status_button = 0;
	}
	else if (state==running){
		DIGITAL_IO_SetOutputHigh(&EN_1);
		DIGITAL_IO_SetOutputHigh(&EN_2);
		DIGITAL_IO_SetOutputHigh(&EN_3);
		DIGITAL_IO_SetOutputHigh(&SSR1);//PCR_SW = 1;
		DIGITAL_IO_SetOutputHigh(&SSR2);//PCS_SW = 1;
		SCADA_status_button = 1;
	}

}


void Update_PWM(void){
	DIGITAL_IO_SetOutputHigh(&P_1_0);
	///////////////////   BEGGINING OF PERIODIC CONTROL INTERRUPTION


	/// ADC acquisition  - AC Voltages
	V_abc_adc[0]=ADC_MEASUREMENT_ADV_GetResult(&ADC_MEASUREMENT_1_V1_1);
	V_abc_adc[1]=ADC_MEASUREMENT_ADV_GetResult(&ADC_MEASUREMENT_2_V2_1);
	V_abc_adc[2]=ADC_MEASUREMENT_ADV_GetResult(&ADC_MEASUREMENT_2_V2_3);

	V_abc[0]=(V_abc_adc[0]-(1800.0f + 12.98f)) * 0.720f;
	V_abc[1]=(V_abc_adc[1]-(1800.0f + 2.69f)) * 0.720f;
	V_abc[2]=(V_abc_adc[2]-(1800.0f + 16.69f)) * 0.720f;

	V_abc[0] = LPF1(V_abc[0], ADC_LPFbuff_VA, LPF_K_1500);
	V_abc[1] = LPF1(V_abc[1], ADC_LPFbuff_VB, LPF_K_1500);
	V_abc[2] = LPF1(V_abc[2], ADC_LPFbuff_VC, LPF_K_1500);

	/// ADC acquisition  - AC Currents
	I_abc_adc[0]=ADC_MEASUREMENT_ADV_GetResult(&ADC_MEASUREMENT_2_V2_2);
	I_abc_adc[1]=ADC_MEASUREMENT_ADV_GetResult(&ADC_MEASUREMENT_1_V1_4);
	I_abc_adc[2]=ADC_MEASUREMENT_ADV_GetResult(&ADC_MEASUREMENT_1_V1_3);

	I_abc[0]=(I_abc_adc[0]-(1800.0f - 18.18f)) * 0.022f;
	I_abc[1]=(I_abc_adc[1]-(1800.0f - 15.91f)) * 0.022f;
	I_abc[2]=(I_abc_adc[2]-(1800.0f - 19.55f)) * 0.022f;

	I_abc[0] = LPF1(I_abc[0], ADC_LPFbuff_IA, LPF_K_1500);
	I_abc[1] = LPF1(I_abc[1], ADC_LPFbuff_IB, LPF_K_1500);
	I_abc[2] = LPF1(I_abc[2], ADC_LPFbuff_IC, LPF_K_1500);

	/// ADC acquisition  - DC BUS Voltage
	V_DC_adc = ADC_MEASUREMENT_ADV_GetResult(&ADC_MEASUREMENT_1_V1_2);
	V_DC = (V_DC_adc-(1800.0f + 9.7f)) * -0.58f;

	conv.Vdc = LPF1(V_DC, LPFbuff_vdc, LPF_K_100);

	/// ADC acquisition  - Converter temperature
	termistor_temp = ADC_MEASUREMENT_ADV_GetResult(&ADC_MEASUREMENT_3_V3_1);
	float conv_temperature = termistor_temp; //auxiliar variable to avoid multiple
	conv_temp_C =       (conv_temperature*conv_temperature*-0.00016973) +  //x^2
			(conv_temperature*0.69969095) +  //x^1
			-653.10731030;  //x^0 */
	conv_temp_C += 7.0f;  //compensação para temperatura da junção

	conv.temp = LPF1(conv_temp_C, LPFbuff_temp, LPF_K_1);


	///  micrium scope variables
	scope_adc7 = V_DC;
	scope_adc1 = I_abc[0]; scope_adc2 = I_abc[1]; scope_adc3 = I_abc[2];
	scope_adc4 = V_abc[0]; scope_adc5 = V_abc[1]; scope_adc6 = V_abc[2];

	////////////////////////////////////////   PLACE CONVERTER CONTROL HERE


	///// begin PLL
	QSG(V_abc[2], dqsg.w, &(dqsg.QSG_d));
	SOGI_v_AB[0] = dqsg.QSG_d.v_AB[0];
	SOGI_v_AB[1] = dqsg.QSG_d.v_AB[1];//*(w_aux/(100.0f*PI));
	SOGI_v_AB[1] *= (PLL_w / PLL_w0);

	AB_dq(SOGI_v_AB, PLL_Vdq, PLL_wt);
	PLL_Vdq[0] = LPF1(PLL_Vdq[0], PLL_LPFbuff_d, LPF_K_500);
	PLL_Vdq[1] = LPF1(PLL_Vdq[1], PLL_LPFbuff_q, LPF_K_500);
	conv.Vdq[0] = PLL_Vdq[0];
	conv.Vdq[1] = PLL_Vdq[1];

	PLL_w = PI_TR_p(PLL_Vdq[1], Ts, &PI_PLL) + PLL_w0;
	PLL_wt = fw_integ(PLL_w, &PLL_wt_buff, Ts, PI2);
	PLL_w = LPF1(PLL_w, PLL_LPFbuff_w, LPF_K_10);
	conv.wt = PLL_wt + ((PLL_w*PLL_w - PLL_w0*PLL_w0)/(1.4142136f*PLL_w0*PLL_w));
	///// end PLL

	///// begin CTRL: Idq transform
	i_dqsg.w = dqsg.w;
	QSG(I_abc[0], i_dqsg.w, &(i_dqsg.QSG_d));
	SOGI_i_AB[0] =  i_dqsg.QSG_d.v_AB[0];
	SOGI_i_AB[1] =  i_dqsg.QSG_d.v_AB[1];
	AB_dq(SOGI_i_AB, CTRL_idq, PLL_wt);
	///// end CTRL: Idq transform
	
	/////////////////////   switch MODO controlo barramento
/*     VDC_BUS_REF = 200.0f; //SCADA_Vdc_ref; 							//recebe referência do micrium/CAN
     //vdc_bus_error = ((VDC_BUS_REF)-(conv.Vdc));						//calcula erro para PI: tensão  
     vdc_bus_error = ((VDC_BUS_REF*VDC_BUS_REF)-(conv.Vdc*conv.Vdc));	//calcula erro para PI: ENERGIA dc_bus
     vdc_bus_error = (state == running) ? vdc_bus_error : 0;			//hold ao erro se não estiver em running
     vdc_bus_piout = -PI_TR_p(vdc_bus_error, Ts, &PI_Vdc); 				//PI CTRL tensão barramento DC
     I_dq_ref[0] = vdc_bus_piout;										//passa referência corrente activa para transf Idq->IAB 

    CTRL_idq_ref[1] = (state == running) ? SCADA_Iq_ref : 0;			//recebe referência do micrium/CAN
    CTRL_idq_ref[1] = (CTRL_idq_ref[1] < -5) ? -5 : CTRL_idq_ref[1]; 	//saturação
    CTRL_idq_ref[1] = (CTRL_idq_ref[1] > 5)  ?  5 : CTRL_idq_ref[1]; 	//saturação
    //CTRL_idq_ref[1] = (state == running) ? 0 : 0;					
     I_dq_ref[1] = PI_TR_p(CTRL_idq_ref[1] - CTRL_idq[1], Ts, &PI_q);	//PI CTRL corrente reactiva
*/
    /////////////////////   switch MODO controlo PQ
    CTRL_idq_ref[0] = (state == running) ? SCADA_Id_ref : 0;   			//recebe referência do micrium/CAN
    CTRL_idq_ref[0] = (CTRL_idq_ref[0] < 0) ? 0 : CTRL_idq_ref[0];  	//saturação !!!!!!!!!!!!  se barramento=rectificador -> min=0
    CTRL_idq_ref[0] = (CTRL_idq_ref[0] > 5) ? 5 : CTRL_idq_ref[0];  	//saturação
    //CTRL_idq_ref[0] = (state == running) ? 0 : 0;

    CTRL_idq_ref[1] = (state == running) ? SCADA_Iq_ref : 0;			//recebe referência do micrium/CAN
    CTRL_idq_ref[1] = (CTRL_idq_ref[1] < -5) ? -5 : CTRL_idq_ref[1]; 	//saturação
    CTRL_idq_ref[1] = (CTRL_idq_ref[1] > 5)  ?  5 : CTRL_idq_ref[1]; 	//saturação
    //CTRL_idq_ref[1] = (state == running) ? 0 : 0;
	I_dq_ref[0] = PI_TR_p(CTRL_idq_ref[0] - CTRL_idq[0], Ts, &PI_d);	//PI CTRL corrente activa
	I_dq_ref[1] = PI_TR_p(CTRL_idq_ref[1] - CTRL_idq[1], Ts, &PI_q);  	//PI CTRL corrente reactiva

	/////////////////////   END switch

	///// begin Idq to AB references transform
	dq_AB(I_dq_ref, I_AB, conv.wt);										//transf Idq->IAB
    I_AB[0] = (state == running) ? I_AB[0] : 0;							//passa referência para PR
    ///// end Idq to AB references transform

	///// begin PR_ctrl
	set_PR_ref(&PR_Test, I_AB[0]);										//Atribui Ialfa como referêcia p/ PR
	Iu_filt = LPF1(I_abc[0], PR_LPFbuff_Iu, LPF_K_500);					//Filtragem !!!!!!!!!  Ja feita acima
	PR_output = Calc_prStruct(&PR_Test, Iu_filt, 100.0f*PI) ;			//Corre PR CTRL

	PR_output = (state == running) ? PR_output : 0;						//passa referência para modulação
	PR_output = (PR_output >  15.0f) ?  15.0f : PR_output;				//satura saída
	PR_output = (PR_output < -15.0f) ? -15.0f : PR_output;				//satura saída

	//PR_output = 0.0f;
	vdc_division = (conv.Vdc < 10) ? 10 : conv.Vdc;   					//permitir divisão por 0
	vdc_division *= 2.0f;  // ganho do transformador					//!!!!!!!!!  UMA VEZ QUE MEDIDA Vac É NO PRIMÁRIO DO TRANSFORMADOR, ENTÃO É COLOCADO AQUI UMA "ESTIMATIVA" DO GANHO

	m_u = (PR_output + SOGI_v_AB[0]) / (vdc_division);					//MODULAÇÃO: soma Va_PLL a PR_out
	m_v = -m_u;															//Gera a referência p/ segundo braço

	vmabc[0] = m_u * 1.0f;												//A RETIRAR
	vmabc[1] = m_v * 1.0f;												//A RETIRAR


	for (int i=0; i<3; i++){
		vmabc[i]=fminf(vmabc[i],0.97f);
		vmabc[i]=fmaxf(vmabc[i],-0.97f);
		// Convert float to uint32 voltage modulator wave
		m_abc[i]=((int32_t)(10000.0f*vmabc[i])>>1)+5000u;
	}

	///  micrium scope variables
	scopeu1=m_abc[0];
	scopeu2=m_abc[1];
	scopeu3=m_abc[2];

	// update PWM duty cycles
	PWM_SetDutyCycle(&PWM_a,m_abc[0]);
	PWM_SetDutyCycle(&PWM_b,m_abc[1]);
	PWM_SetDutyCycle(&PWM_c,m_abc[2]);

	ConverterStateMachine();

	///////////////////   END OF PERIODIC CONTROL INTERRUPTION
	DIGITAL_IO_SetOutputLow(&P_1_0);
}

int main(void)
{
	DAVE_STATUS_t status;
	status = DAVE_Init();           /* Initialization of DAVE APPs  */
	if(status != DAVE_STATUS_SUCCESS)
	{
		/* Placeholder for error handler code. The while loop below can be replaced
		 * with an user error handler. */
		XMC_DEBUG("DAVE APPs initialisation failed\n");
		while(1U){}
	}
	ProbeScope_Init(SystemCoreClock/TICKS_PER_SECOND);   /// for micrium uScope


	/////////////   DISABLE OUPUTS
	DIGITAL_IO_SetOutputLow(&ENABLE);
	DIGITAL_IO_SetOutputLow(&FAULT_RST);

	DIGITAL_IO_SetOutputLow(&EN_1);
	DIGITAL_IO_SetOutputLow(&EN_2);
	DIGITAL_IO_SetOutputLow(&EN_3);

	PWM_Stop(&PWM_a);
	PWM_Stop(&PWM_b);
	PWM_Stop(&PWM_c);

	////////////   ENABLE OUTPUTS/TIMERS
	PWM_Start(&PWM_update);
	PWM_Start(&PWM_a);
	PWM_Start(&PWM_b);
	PWM_Start(&PWM_c);



	////////////  SET GLOBAL VARS HERE
	Init_prStruct(&PR_Test, PR_Kp, PR_Kr, PR_Wi);

	while(1U)
	{
		///////////   IMPLEMENT STATE MACHINE HERE
		//ConverterStateMachine();
		//////////   END OF STATE MACHINE
		ProbeScope_Sampling();    /// for micrium uScope
	}
}

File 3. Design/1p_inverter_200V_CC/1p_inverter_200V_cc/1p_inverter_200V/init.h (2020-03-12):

// v10.3
// Updated in 07/06/2019

// for microProbe
	#define TICKS_PER_SECOND (10000u)
	float Vdc_error=0.0f;

// math constants
	#define PI32 4.7123890f			// 3/2*PI
	#define PI2 6.2831853f			// 2*PI
	#define K23 0.66666667f			// 2/3
	#define Ksqr32 0.86602540f		// sqrt(3)/2
	#define K23sqr3 0.38490018f		// 2/(3*sqrt(3))

// system constants
	#define fs 5000.000f
	#define Ts 0.00010000f
	#define wL 3.3600000f			// =100*pi*10.7e-3 //=100*pi*(1.25e-3*2) //=100*pi*5.2e-3
	#define R 2.5600000f
	#define Kp_PLL 1.370000f
	#define Ki_PLL 163.00000f
	#define Kp_I 2.5600000f
	#define Ki_I 1225.0000f
	#define kd 0.00100000f
	#define td 0.06600000f
	#define Kp_V_DC 0.0003//0.311111f
	#define Ki_V_DC 0.006 //20.1707f
	#define TIMER_DELAY_INIT 1*1000000u		//Scaling the required values by 100000.
	#define TIMER_K1 4*1000000u				//Scaling the required values by 100000.
	#define TIMER_K2 10*1000000u			//Scaling the required values by 100000.
	#define TIMER_OPEN_K1_K2 5*1000000u		//Scaling the required values by 100000.
	#define ma_max 0.970000f				// Maximum modulation index
	const uint32_t chargeTime=2000000;

	#define _1MS 10

// conversion constants

	struct ADC_config {
		float conv;		// 0.00080586f (value* 3.3/4095) uint to real voltage
		float offset;	// 1.6500000f (value* 3.3/2) ac quantity offset
		float toVac;	// 386.814f (2/(15/230*536/(536+3480))*0.58) convert to AC voltage
		float toVdc;	// 0.247897f (value* 800/3.3*3.3/4096) convert to DC bus voltage
		float toIac;	// 29.6875f (value* 50/3.205*(1.9)) convert to AC line currents
	};
	struct ADC_config ADC={0.00080586f, 1.6500000f, 386.814f*0.9f, 0.195313f, 29.6875f};

	// 1st order filters constants
	#define wo_LPF_1 6.28319f		// LPF cutoff frequency- 1 Hz
	#define wo_LPF_10 78.5398f		// LPF cutoff frequency- 12.5 Hz
	#define wo_LPF_50 314.159f		// LPF cutoff frequency- 50 Hz
	#define wo_LPF_100 628.319f		// LPF cutoff frequency- 100 Hz
	#define wo_LPF_500 3455.75f		// LPF cutoff frequency- 550 Hz (3455.75f)
	#define wo_LPF_1500 9424.78f	// LPF cutoff frequency- 1500 Hz
	#define wo_LPF_Iref 314.159f	// LPF cutoff frequency- 50 Hz

	const float K_sync[4]={50000.0f, 0.75f, 10.0f};
	const float PI_K_CC[2]={Kp_I, Ki_I};
	const float HPF_K[4]={kd*td, -kd*td, td, td-Ts};
	// LPF_K_X[3]={k, a0/b1, -b0/b1}
	const float LPF_K_1[3]={1, Ts*wo_LPF_1/(2+Ts*wo_LPF_1), -(Ts*wo_LPF_1-2)/(2+Ts*wo_LPF_1)};
	const float LPF_K_10[3]={1, Ts*wo_LPF_10/(2+Ts*wo_LPF_10), -(Ts*wo_LPF_10-2)/(2+Ts*wo_LPF_10)};
	const float LPF_K_50[3]={1, Ts*wo_LPF_50/(2+Ts*wo_LPF_50), -(Ts*wo_LPF_50-2)/(2+Ts*wo_LPF_50)};
	const float LPF_K_100[3]={1, Ts*wo_LPF_100/(2+Ts*wo_LPF_100), -(Ts*wo_LPF_100-2)/(2+Ts*wo_LPF_100)};
	const float LPF_K_500[3]={1, Ts*wo_LPF_500/(2+Ts*wo_LPF_500), -(Ts*wo_LPF_500-2)/(2+Ts*wo_LPF_500)};
	const float LPF_K_1500[3]={1, Ts*wo_LPF_1500/(2+Ts*wo_LPF_1500), -(Ts*wo_LPF_1500-2)/(2+Ts*wo_LPF_1500)};

// Structures:

	struct Config {
		float Vdc_max;
		float Vdc_min;
		float Vd_max;
		float Vd_min;
		float w_max;
		float w_min;
		float I_max;
		float I_min;
		float S_max; 	// maximum apparent power
	};
	// struct Config conf={Vdc_max, Vdc_min, 1.15pu, 0.85pu, 51.5Hz, 47.5Hz, Imax};
	// struct Config conf={750.0f, 400.0f, 374.06f, 276.47f, 323.59f, 298.45f, 70.0f, -70.0f, 30000.0f};
	struct Config conf={750.0f, 350.0f, 374.06f, 276.47f, 323.59f, 298.45f, 15.0f, -15.0f, 5000.0f};

	// This structure keeps the converter vars after filtering:
	struct ConverterVars {
		float Idq[2];
		float PQ[2];
		float Vdc;
		float Vdq[2];
		float w;
		float wt;
		float temp;
	};
	struct ConverterVars conv={{0.0f, 0.0f},{0.0f, 0.0f}, 0.0f, {0.0f, 0.0f}, 0.0f, 0.0f, 0.0f};

	struct LPF1_dq {
		const float K[3]; 	// a0, b1, b0
		float buff[4];		// buffer for last values and filter accumulator of both quantities
	};
	struct LPF1_dq LPF_idq_ref={{1, Ts*wo_LPF_50/(2+Ts*wo_LPF_50), -(Ts*wo_LPF_50-2)/(2+Ts*wo_LPF_50)},{0.0f, 0.0f, 0.0f, 0.0f}};
	struct LPF1_dq LPF_iAB={{1, Ts*wo_LPF_500/(2+Ts*wo_LPF_500), -(Ts*wo_LPF_500-2)/(2+Ts*wo_LPF_500)},{0.0f, 0.0f, 0.0f, 0.0f}};
	struct LPF1_dq LPF_vAB={{1, Ts*wo_LPF_500/(2+Ts*wo_LPF_500), -(Ts*wo_LPF_500-2)/(2+Ts*wo_LPF_500)},{0.0f, 0.0f, 0.0f, 0.0f}};

	// Bilinear discretization:
	struct LPF2 {
			const float K[6]; 	// a0, a1, a2, b0, b1, 1/b2
			float buff[4];		// buffer for last values and filter accumulator of both quantities
		};
	#define LPF_zeta 0.707107f
	struct LPF2 LPF2_K_10={{wo_LPF_10*wo_LPF_10*Ts*Ts, 2*wo_LPF_10*wo_LPF_10*Ts*Ts, wo_LPF_10*wo_LPF_10*Ts*Ts, Ts*Ts*wo_LPF_10*wo_LPF_10+4-4*LPF_zeta*wo_LPF_10*Ts, 2*Ts*Ts*wo_LPF_10*wo_LPF_10-8, 1/(wo_LPF_10*wo_LPF_10*Ts*Ts+4*LPF_zeta*wo_LPF_10*Ts+4)},{0.0f, 0.0f, 0.0f, 0.0f}};
	struct LPF2 LPF2_K_50={{wo_LPF_50*wo_LPF_50*Ts*Ts, 2*wo_LPF_50*wo_LPF_50*Ts*Ts, wo_LPF_50*wo_LPF_50*Ts*Ts, Ts*Ts*wo_LPF_50*wo_LPF_50+4-4*LPF_zeta*wo_LPF_50*Ts, 2*Ts*Ts*wo_LPF_50*wo_LPF_50-8, 1/(wo_LPF_50*wo_LPF_50*Ts*Ts+4*LPF_zeta*wo_LPF_50*Ts+4)},{0.0f, 0.0f, 0.0f, 0.0f}};
	struct LPF2 LPF2_K_100={{wo_LPF_100*wo_LPF_100*Ts*Ts, 2*wo_LPF_100*wo_LPF_100*Ts*Ts, wo_LPF_100*wo_LPF_100*Ts*Ts, Ts*Ts*wo_LPF_100*wo_LPF_100+4-4*LPF_zeta*wo_LPF_100*Ts, 2*Ts*Ts*wo_LPF_100*wo_LPF_100-8, 1/(wo_LPF_100*wo_LPF_100*Ts*Ts+4*LPF_zeta*wo_LPF_100*Ts+4)},{0.0f, 0.0f, 0.0f, 0.0f}};
	struct LPF2 LPF2_K_500={{wo_LPF_500*wo_LPF_500*Ts*Ts, 2*wo_LPF_500*wo_LPF_500*Ts*Ts, wo_LPF_500*wo_LPF_500*Ts*Ts, Ts*Ts*wo_LPF_500*wo_LPF_500+4-4*LPF_zeta*wo_LPF_500*Ts, 2*Ts*Ts*wo_LPF_500*wo_LPF_500-8, 1/(wo_LPF_500*wo_LPF_500*Ts*Ts+4*LPF_zeta*wo_LPF_500*Ts+4)},{0.0f, 0.0f, 0.0f, 0.0f}};
	struct LPF2 LPF2_K_1500={{wo_LPF_1500*wo_LPF_1500*Ts*Ts, 2*wo_LPF_1500*wo_LPF_1500*Ts*Ts, wo_LPF_1500*wo_LPF_1500*Ts*Ts, Ts*Ts*wo_LPF_1500*wo_LPF_1500+4-4*LPF_zeta*wo_LPF_1500*Ts, 2*Ts*Ts*wo_LPF_1500*wo_LPF_1500-8, 1/(wo_LPF_1500*wo_LPF_1500*Ts*Ts+4*LPF_zeta*wo_LPF_1500*Ts+4)},{0.0f, 0.0f, 0.0f, 0.0f}};

	struct PI_tr_p {
		const float K[2]; 	// Kp Ki
		float sat[2];		// output saturation
		float buff[2];		// (x[n]; yi[n])
		uint8_t flag;
	};
	struct PI_tr_p PI_PLL = {{Kp_PLL, Ki_PLL},{942.47780f, -942.47780f},{0.0f, 0.0f},0u};
	struct PI_tr_p PI_Vdc = {{Kp_V_DC, Ki_V_DC},{15, -15},{0.0f, 0.0f},0u};

	struct PI_tr_p PI_d   = {{0.05f, 40.0f},{15, -15},{0.0f, 0.0f},0u};
	struct PI_tr_p PI_q   = {{0.05f, 40.0f},{15, -15},{0.0f, 0.0f},0u};

	struct PI_dq_tr {
		const float K[2]; 	// Kp Ki
		float sat[2];		// output saturation
		float buff[4];		// [e_d[n-1]; ei_d[n-1]; e_q[n-1]; ei_q[n-1]]
		uint8_t flag;
	};
	struct PI_dq_tr PI_cc={{Kp_I, Kp_I*Ki_I},{710.0f, -700.0f},{0.0f, 0.0f, 0.0f, 0.0f},0u};

	struct sogi {
		float v_AB[2];
		float K;		// sqrt(2)= 1.4142136f
		float dbuff;
		float qbuff;
		const float Ti;
	};

	struct dsogi{
		float w;
		struct sogi QSG_d;
		struct sogi QSG_q;
	};
	struct dsogi dqsg={100.0f*PI, {{0.0f, 0.0f}, 1.4142136f, 0.0f, 0.0f, Ts}, {{0.0f, 0.0f}, 1.4142136f, 0.0f, 0.0f, Ts}};
	struct dsogi i_dqsg={100.0f*PI, {{0.0f, 0.0f}, 1.4142136f, 0.0f, 0.0f, Ts}, {{0.0f, 0.0f}, 1.4142136f, 0.0f, 0.0f, Ts}};
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

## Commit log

2019-09-10 added PCB files and updated README
    [controlo_rev2.PcbDoc, controlo_rev2.PrjPcb, controlo_rev2.SchDoc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]
2019-09-10 "populated" folders with preliminary content
    [BOM.xlsx]
2019-09-11 updated BOM for 5 boards
    [BOM.xlsx]
2019-10-11 added 3ph psim simulation, 1ph psim simulation and updated XMC code
    [BOM.xlsx, BOM_rui.xlsx]
2019-10-29 Major revision
    - Updated code after 3kW 300V testing;
    - Tested temperature measurement;
    - Added CAD files for 3d-print
    - First version of the application note guide
    [7030025_PART_FAN STANDARD 90_MODEL.igs.SLDPRT, 7030026_PART_HEATSINK ADAPTOR 90_MODEL.igs.SLDPRT, BOM.xlsx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]
2019-10-30 Prepare for release
    - Updated guide
    - Updated DAVE repository (with a .zip file to import)
    - Major code review
    - Updated README
    [inversor_rev2.SchDoc]
2019-11-15 added Coil CAD; updated list of material; updated guide; fixed 1p ctrl PR
    [BOM_CAN.xlsx, Lista de Material.xlsx, bobina.SLDPRT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]
2019-11-28 starting to add PSIM code
    [PN.NOR.0102-V1.stp, PN.NOR.0117-V1.stp, PN.NOR.SLDPRT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]
2019-12-08 started PCB REV.3
    [1054311103.step, controlo_rev2.PcbDoc, controlo_rev2.PrjPcb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]
2019-12-11 Started middle PCB - first iteration
    [Calculos.xlsx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]
2019-12-15 Completed alfa version of REV 3.0
    developed 3 boards plus the CAD asm
    [XMC4500.dxf, controlo_rev3.PcbDoc, controlo_rev3.PrjPcb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]
2019-12-19 ammendment on PCBs and preliminary CAD generation
    [controlo_rev3.PrjPcb, controlo_rev3.xls, existências.xlsx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]
2019-12-28 final amendment on REV3.0
    [470533000.stp, 879370800.stp, BOM.xlsx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]
2020-01-03 updated BOM on schematics
    [BOM.xlsx, Orçamento.xlsx, controlo_rev3.CSV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]
2020-01-03 Added DC_BUS extra connectors; added DC bus MLCC caps
    [inversor_rev3.PcbDoc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]
2020-01-07 hardware: minor_changes; tuned 200V DC-bus; started 400V tuning.
2020-01-07 tunned 400V
2020-01-11 Added reactive power control; added voltage grid:sags+harmonics
    [GLOBAL_functions.h, dc_ac_1ph_code.cpp]
2020-01-14 1. added decoupled dq current PI's; 2. added grid noise; 3. tunned all PI's
    [GLOBAL_functions.h, dc_ac_1ph_code.cpp]
2020-01-17 Final 400V DCBUS ctrl tuning!!
2020-01-17 Prepared DAVE 200V code
2020-01-23 1. Updated PCB's gerbers; 2. exported STEP 3d files
    [BOM.xlsx, controlo_rev3.CSV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]
2020-01-24 revision before powercut
    [inversor_rev3.PcbDoc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]
2020-03-12 major revision REV4.0
    [BOM.xlsx, BOM_REV4.xlsx, Calibração.xlsx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]
2020-04-03 bom update; pc feup commit
    [BOM_REV4.xlsx, measurement_rev4.PcbDoc, measurement_rev4.SchDoc]
2020-04-03 major_update: pc portátil hp
    [BUS_Board.PcbDoc, BUS_Board.PrjPcb, BUS_Board.SchDoc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]
2020-07-23 REV4 final revision
    [+VDC_plane.csv, +VDC_plane_bot.csv, -VDC_plane.csv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]
